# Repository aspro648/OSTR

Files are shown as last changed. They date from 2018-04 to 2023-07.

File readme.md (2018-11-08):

Open Source Turtle Robot (OSTR)
-------------------------------

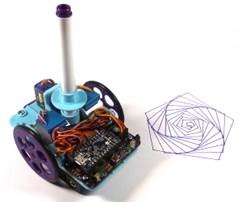
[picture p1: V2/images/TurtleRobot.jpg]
ChickTech Robot
 
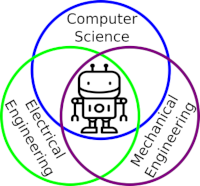
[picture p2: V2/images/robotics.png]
Robotics Engineering Fields
 

I designed this project for a 10-hour workshop for [ChickTech.org](http://www.chicktech.org) whose goal is to introduce teenage women to STEM topics. The goals for this project were:

- Easy to build.
- Easy to program.
- Did something interesting.
- Low-cost so participants could take it home and continue to learn.

Robotics is the exciting intersection of a number of engineering fields including mechanical engineering, electrical engineering, and computer science. This project was designed to make learning about these fields accessible and exciting.

Turtle robots are controled by simple instructions like "forward(distance)" and "left(degrees)", and their visual tracks are instructive as well as entertaining. They also demonstrate how systems with simple rules can have complex behaviors, something we see in nature all the time.

New to Version 2 is the shift from the Adafruit [Trinket Pro](https://www.adafruit.com/product/2010) to their [ItsyBitsy 32U4 3V](https://www.adafruit.com/product/3675) which enables USB communication for easier troubleshooting, or the [ItsyBitsy M0 Express](https://www.adafruit.com/product/3727) which allows programing in Python!

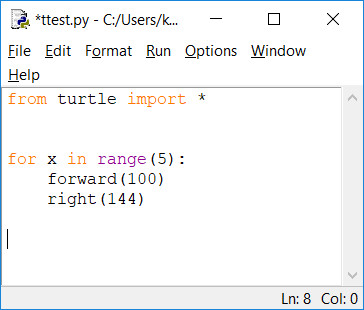
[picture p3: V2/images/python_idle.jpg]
Turtle Python commands in Idle
 
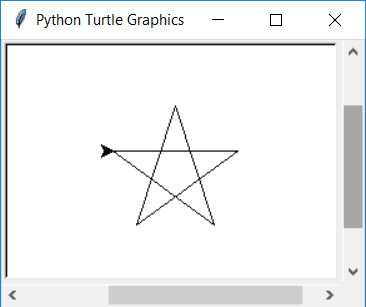
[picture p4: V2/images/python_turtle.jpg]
Turtle Graphics
 

Python is a popular and easy to learn programming language that already has Turle Graphics built in.  Since the robots instructions are the same, programs and paterns can be evaluated on the computer and then run on the robot. 
```python
from turtle import *

for x in range(5):
    forward(100)
    right(144)
```

Here is a great Hour of Code tutorial to get you introduced to Python Turtle: [https://groklearning.com/hoc/activity/snowflake/](https://groklearning.com/hoc/activity/snowflake/).  The only thing pysical Turtle Robot can't do is change colors automatically, but you can alway swap the pens around manually.

### Video of Turtle Robot (V1) in action:

IMAGE ALT TEXT HERE (https://www.youtube.com/watch?v=j0FpB0iv0v0)

This robot has been refined through a number workshops, but still has room for improvement.  Please share your ideas and modifications so it can continue to improve.

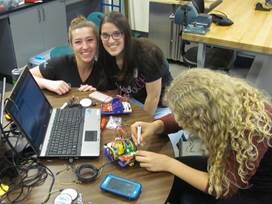
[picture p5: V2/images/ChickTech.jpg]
ChickTech Workshop
 

Bill Of Materials
-----------------
In bulk quantities, the cost per robot is about $40.  The Bill of Materials is available [here](/V2/BOM.md).
Having told you the at-cost and provided you my BOM, I'd still offer to [sell you a kit](https://www.tindie.com/products/MakersBox/open-source-turtle-robot-ostr/) if you'd like to pay for the convenience of a single-source or you don't have access to a 3D printer.  This also allows me continue development for future workshops.

Tindie

Design Files
------------
The electronics were designed using Open Source [KiCad](http://kicad-pcb.org/). Design files are located in the [design_files](V2/design_files/) folder.  You can oogle the [schematic](V2/docs/Schematic.pdf).

The 3D Design files were created with a combination of [FreeCad](https://www.freecadweb.org/), [OpenSCAD](https://www.openscad.org/) (both Open Source), and online [TinkerCad](https://www.tinkercad.com/).  Design files and STLs are located in the [3D](V2/3D/) folder.

Firmware
--------
This project is programed using Open Source [Arduino](https://www.arduino.cc/) or Adafruit's [Circuit Python](https://learn.adafruit.com/welcome-to-circuitpython/what-is-circuitpython) depending on the microcontroller used. The firmware is located in the [firmware](V2/firmware/) folder.  Instructions for setting up the Arduino environment for the ItsyBitsy 32U4 are at [https://learn.adafruit.com/introducting-itsy-bitsy-32u4/](https://learn.adafruit.com/introducting-itsy-bitsy-32u4/).

Assembly Instructions
---------------------
[https://www.instructables.com/id/OSTR/](https://www.instructables.com/id/OSTR/).  
Also, check the [docs](V2/docs/) folder for handouts, etc.  May still have pictures of V1 assembly, but they are nearly identical.

License
-------
[Attribution-ShareAlike 3.0 United States (CC BY-SA 3.0 US)](https://creativecommons.org/licenses/by-sa/3.0/us/)

You are free to:

- Share — copy and redistribute the material in any medium or format
- Adapt — remix, transform, and build upon the material

Under the following terms:

- Attribution — You must give appropriate credit, provide a link to the license, and indicate if changes were made. You may do so in any reasonable manner, but not in any way that suggests the licensor endorses you or your use.
- ShareAlike — If you remix, transform, or build upon the material, you must distribute your contributions under the same license as the original.

Certified Open Source:
----------------------
This project as been certified by the [Open Source Hardward Association](https://certification.oshwa.org/):

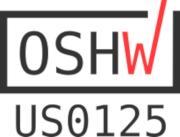
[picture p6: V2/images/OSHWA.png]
OSHWA


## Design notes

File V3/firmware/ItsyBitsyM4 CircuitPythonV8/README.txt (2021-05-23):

Turtle Robot (V2.2) https://github.com/aspro648/OSTR/
@TheMakersBox
#TurtleRobot
648.ken@gmail.com

You have an Adafruit ItsyBitsy M4:
    https://learn.adafruit.com/introducing-adafruit-itsybitsy-m4
Running CiruitPython version 6.2.0
    https://circuitpython.org/board/itsybitsy_m4_express/
With libraries from adafruit-circuitpython-bundle-6.x-mpy-20210521.zip:
    https://github.com/adafruit/Adafruit_CircuitPython_Bundle/releases
Download Mu Editor at https://codewith.mu/en/download

Workshop Links:
  Handouts: https://github.com/aspro648/OSTR/raw/master/V2/docs/Robotics_Handouts.pdf
  Mechanical Assembly: https://github.com/aspro648/OSTR/raw/master/V2/docs/Mechanical_Assembly.pdf
  Name Plate Design: https://github.com/aspro648/OSTR/raw/master/V2/docs/Name_Plate_3D_Design.pdf

Activites:
  https://groklearning.com/hoc/activity/snowflake/
  https://studio.code.org/s/frozen/stage/1/puzzle/1

#############################
CircuitPython Quick Start:

Changing the code is as easy as editing code.py in your favorite text editor. 

Our recommended editor is Mu, which is great for simple projects, and comes
with a built in REPL serial viewer! It is available for Mac, Windows & Linux
https://learn.adafruit.com/welcome-to-circuitpython/installing-mu-editor

After the file is saved, CircuitPython will automatically reload the latest 
code. Try enabling the single-button keyboard!
         (HINT: look for the "# optional! uncomment below..." text)

Connecting to the serial port will give you access to sensor information, 
better error messages and an interactive CircuitPython (known as the REPL). 
On Windows we recommend Mu, Tera Term or PuTTY. 
On Mac OSX and Linux, use Mu or 'screen' can be used from a terminal.

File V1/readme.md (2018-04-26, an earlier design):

Open Source Turtle Robot (OSTR)
============

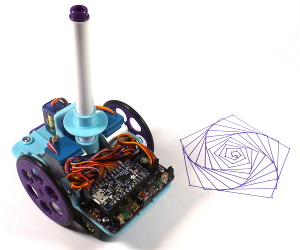
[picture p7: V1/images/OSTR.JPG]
Open Source Turtle Robot
 

Robotics is the exciting intersection of a number of engineering fields including mechanical engineering, electrical engineering, and computer science.  This project was designed as the basis for a two-day workshop for high school age students to introduce them to engineering principles and giving them a jumping off point for exploring their interests further.  There is something for everyone here, even if it is just for the art it creates. The design goals were:

- Easy to build.
- Easy to program.
- Did something interesting.
- Low-cost so participants could take it home and continue to learn.

With those goals in mind, here were a couple of the design choices:

- Arduino compatible for ease of programming.
- 4xAA battery power for cost and availability.
- Stepper motors for accurate motion.
- 3D Printed for ease of customization.
- Pen plotting with Turtle graphics for interesting output.
- Open Source so you could make one of your own!

A kit for this project is [available on Tindie](https://www.tindie.com/products/MakersBox/open-source-turtle-robot-ostr/).
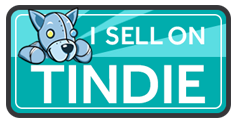
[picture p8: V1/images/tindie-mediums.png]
Tindie Dog (https://www.tindie.com/products/MakersBox/open-source-turtle-robot-ostr/)


Bill Of Materials
-----------------

- [Bill of Materials](BOM.md)

Design Files
------------
The electronics were designed using Open Source [KiCad](http://kicad-pcb.org/). Design files are located in the [electronics](electronics/) folder.  You can oogle the [schematic](electronics/project.pdf).

All 3D STL files located in the [mechanical/STL](mechanical/STL) folder. They were design were designed using:

- [OpenSCAD](http://www.openscad.org/), files located in the [mechanical/OpenSCAD](mechanical/OpenSCAD) folder.
- [FreeCad](https://www.freecadweb.org/), files located in the [mechanical/FreeCad](mechanical/FreeCad) folder.
- [TinkerCad](https://www.tinkercad.com/things/1PzjMSYXagP-oser/editv2) 

Firmware
--------
This project is programed using the Open Source [Arduino](https://www.arduino.cc/). The firmware is located in the [firmware](firmware/) folder.  Instructions for setting up the Arduino enviroment for the Adafruit Trinket Pro are at [https://learn.adafruit.com/introducing-pro-trinket](https://learn.adafruit.com/introducing-pro-trinket).

Assembly Instructions
---------------------
I have published detailed instructions on Instructables at [https://www.instructables.com/id/OSTR/](https://www.instructables.com/id/OSTR/).

License
-------
[Attribution-ShareAlike 3.0 United States (CC BY-SA 3.0 US)](https://creativecommons.org/licenses/by-sa/3.0/us/)

You are free to:

- Share — copy and redistribute the material in any medium or format
- Adapt — remix, transform, and build upon the material

Under the following terms:

- Attribution — You must give appropriate credit, provide a link to the license, and indicate if changes were made. You may do so in any reasonable manner, but not in any way that suggests the licensor endorses you or your use.
- ShareAlike — If you remix, transform, or build upon the material, you must distribute your contributions under the same license as the original.

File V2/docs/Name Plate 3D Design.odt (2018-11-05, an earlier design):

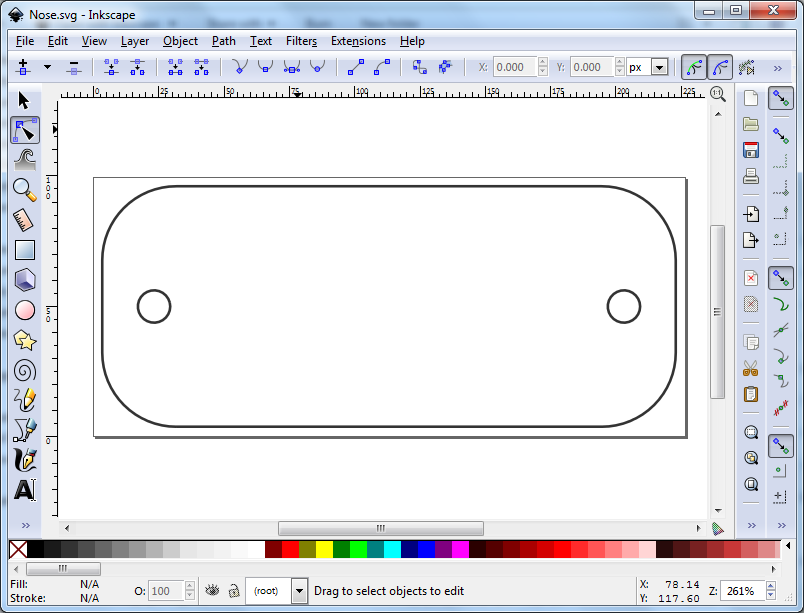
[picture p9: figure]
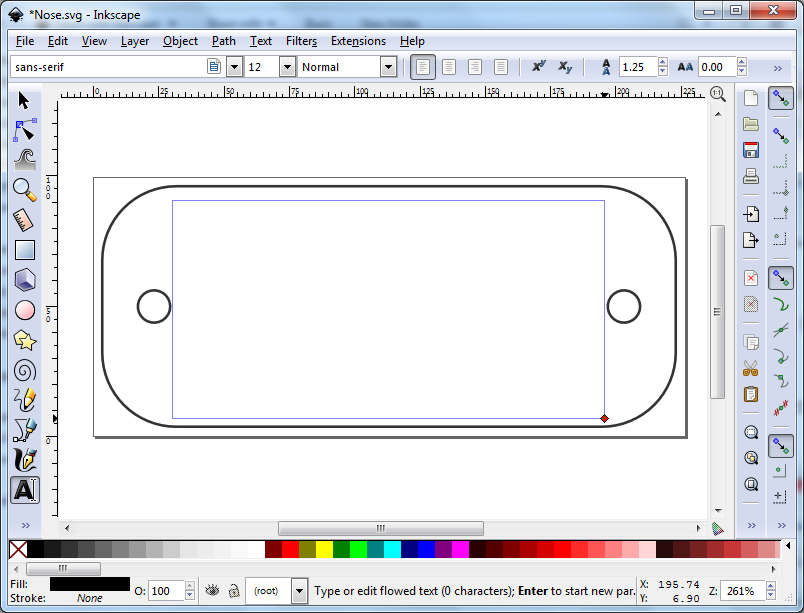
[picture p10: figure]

Launch Inskcape application. Open File “Name_Plate.svg” file. | Click the “A” icon (“Create and Edit Text”) on the left panel and use your mouse to crate a text area within the badge area.

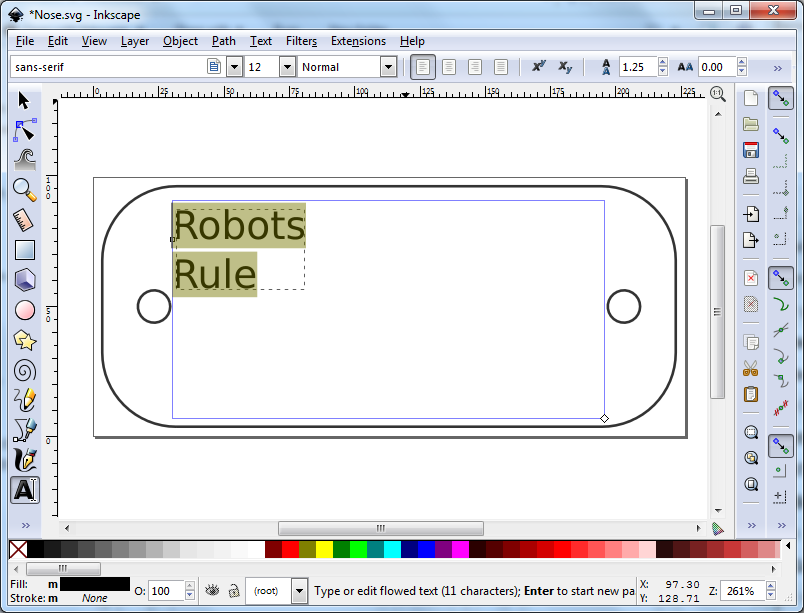
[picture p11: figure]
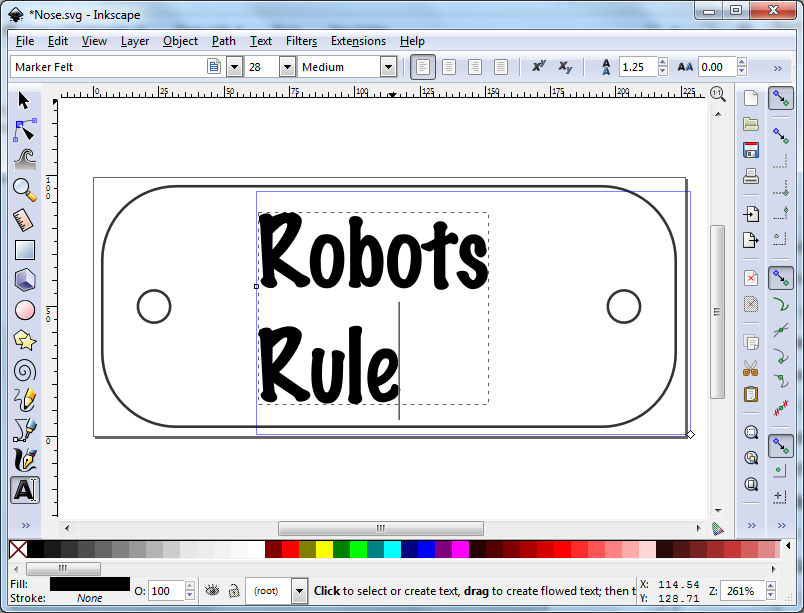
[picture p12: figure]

Type your text in the area. | Select the text with your mouse and then pick the Font and Size you want.

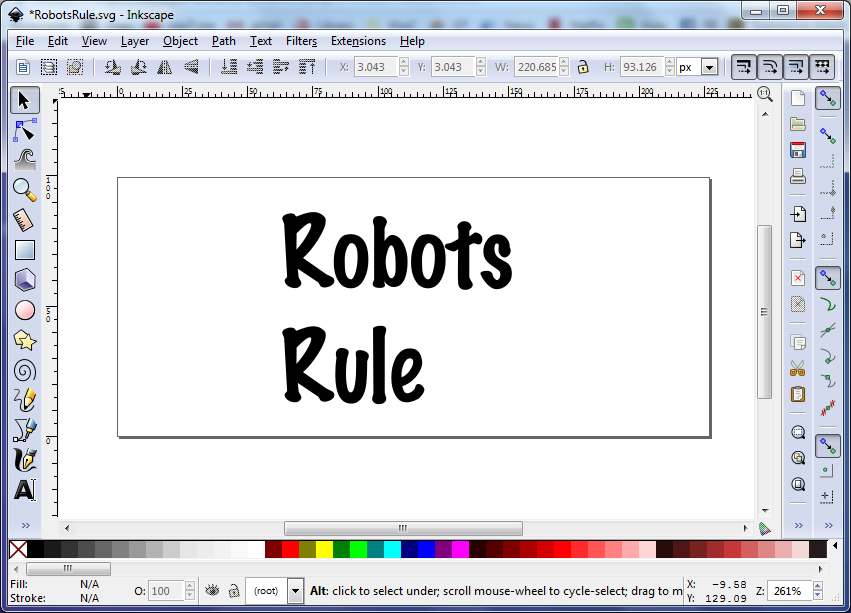
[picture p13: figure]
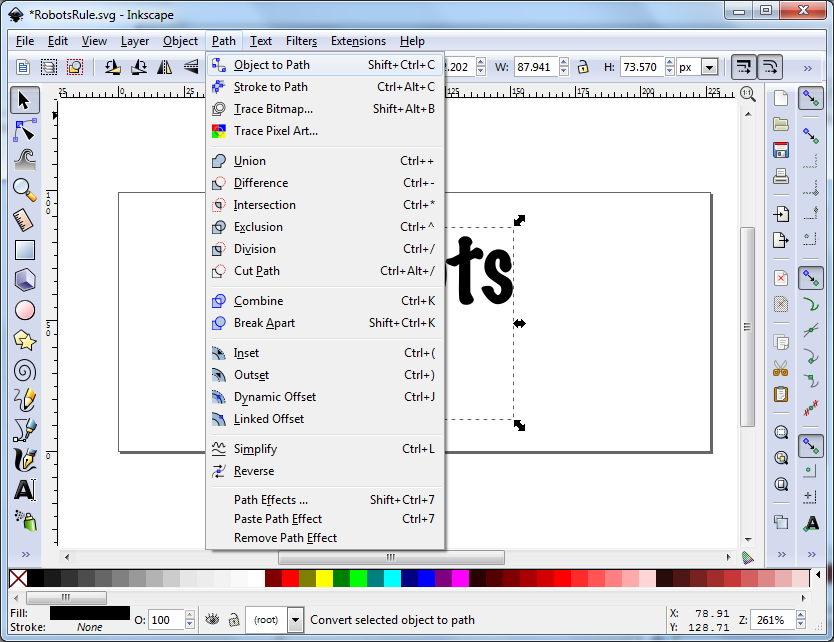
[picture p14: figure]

Select the original badge outline and click delete. “delete”. | Click on the text box again and select “Path” → “Object to Path”.

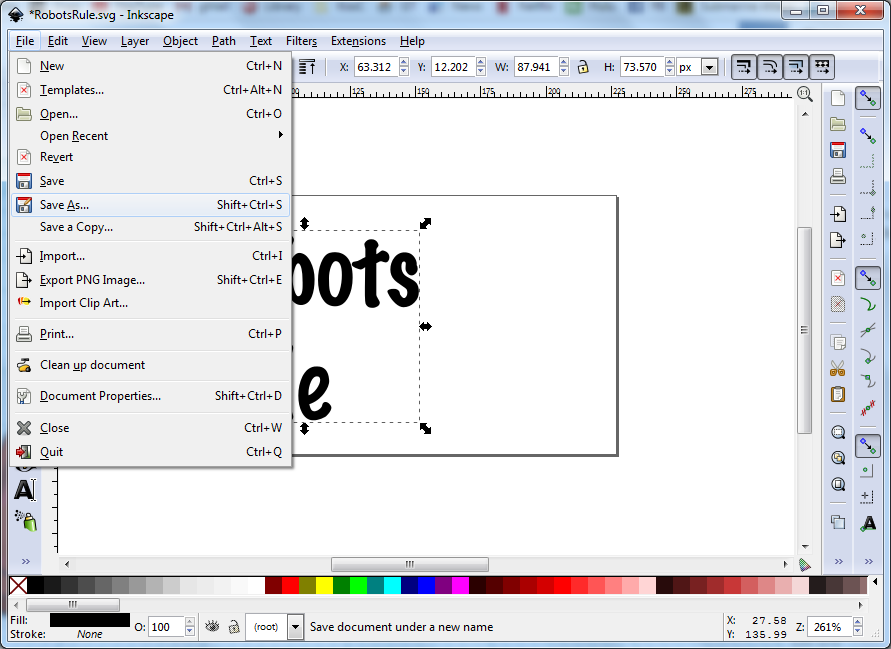
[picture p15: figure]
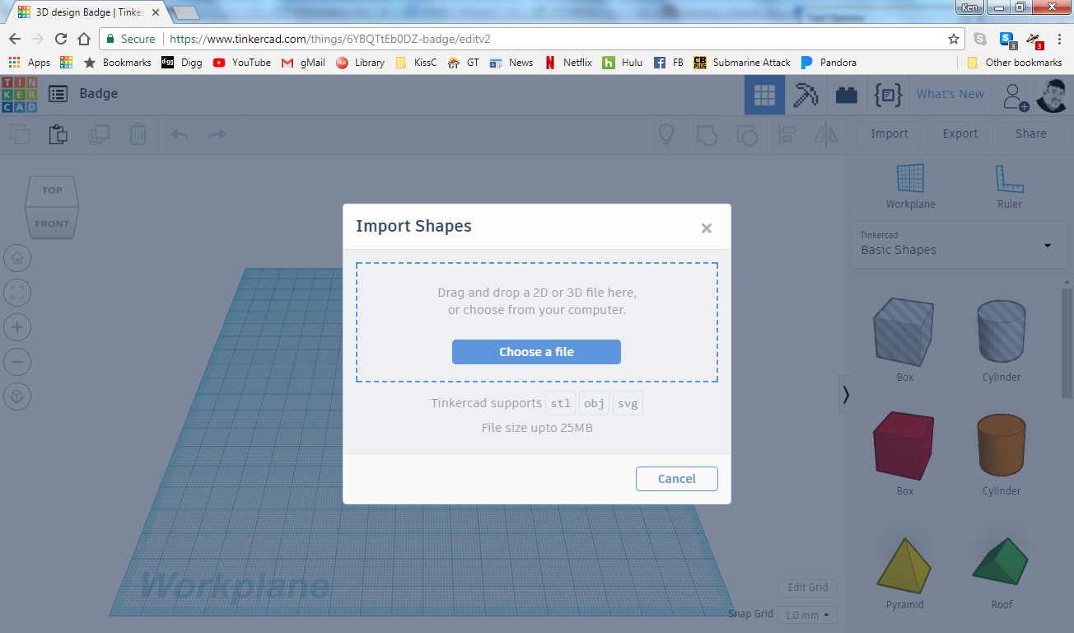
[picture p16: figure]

Select [File] → [Save As] → Select a unique SVG file name. | If needed, sign into TinkerCad.com: User: makers.coderdojo@gmail.com Password: cltm2015 Start a new project. Select [Import] →”Name_Plate.stl”.

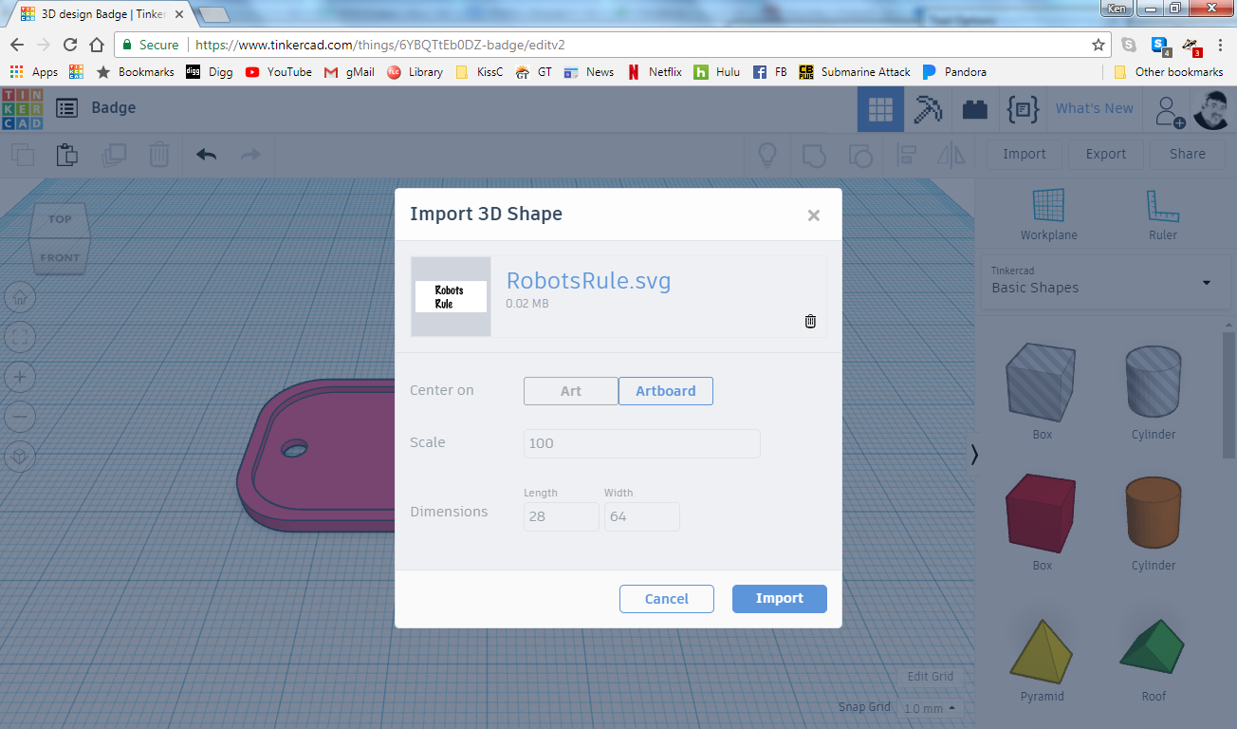
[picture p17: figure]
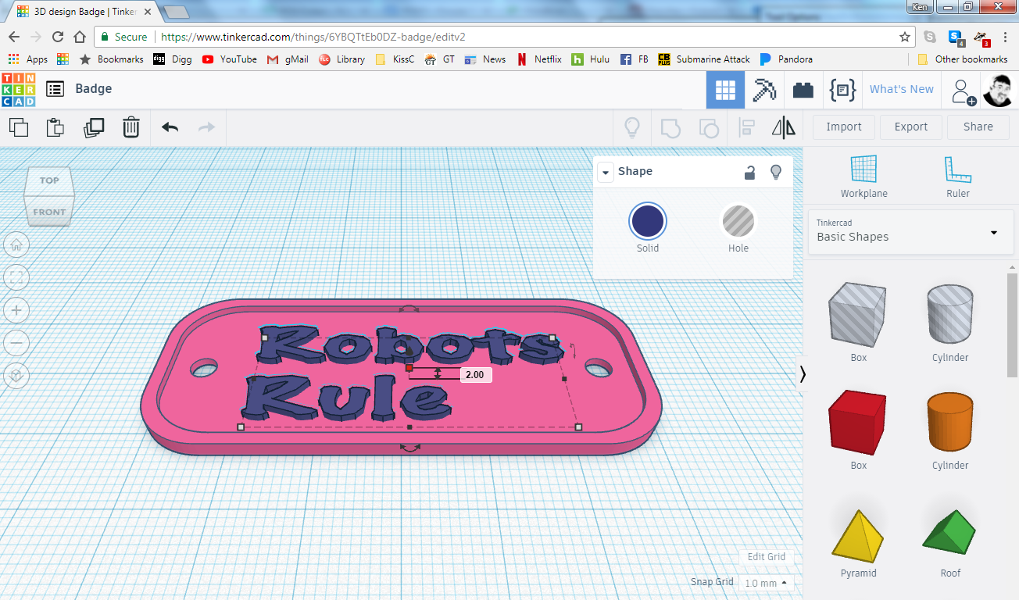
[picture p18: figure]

Select [Import] → Unique svg file you saved earlier. | Repostion and resize text to fit inside of the badge shape. Make the text size 2mm tall.

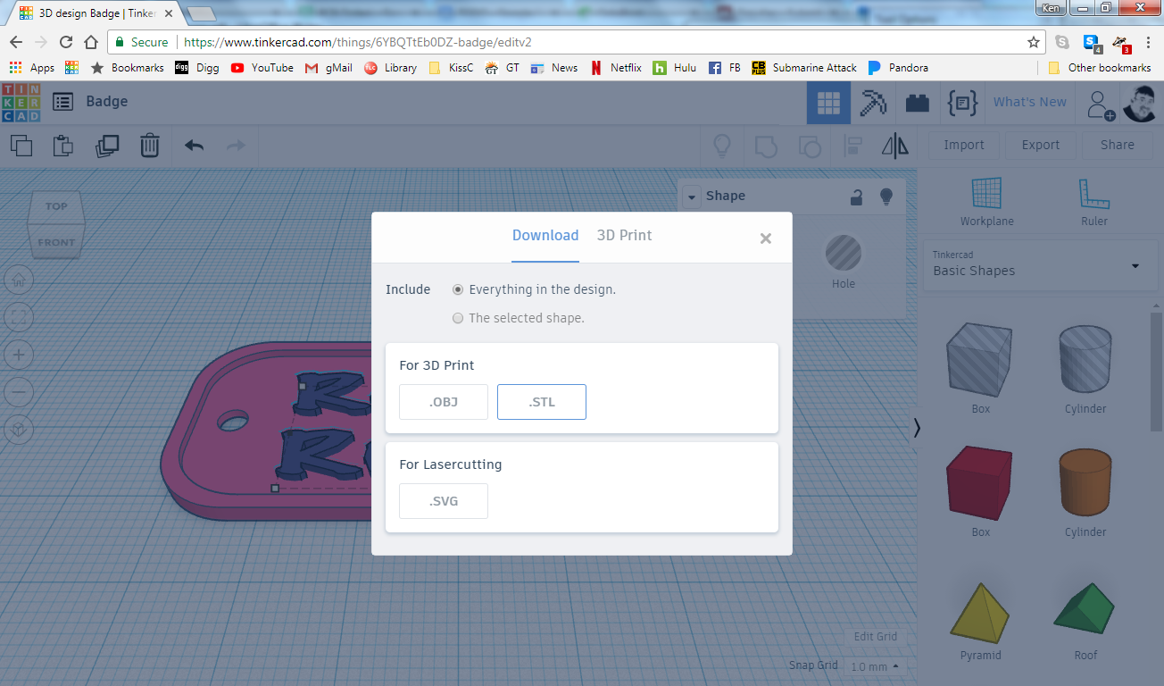
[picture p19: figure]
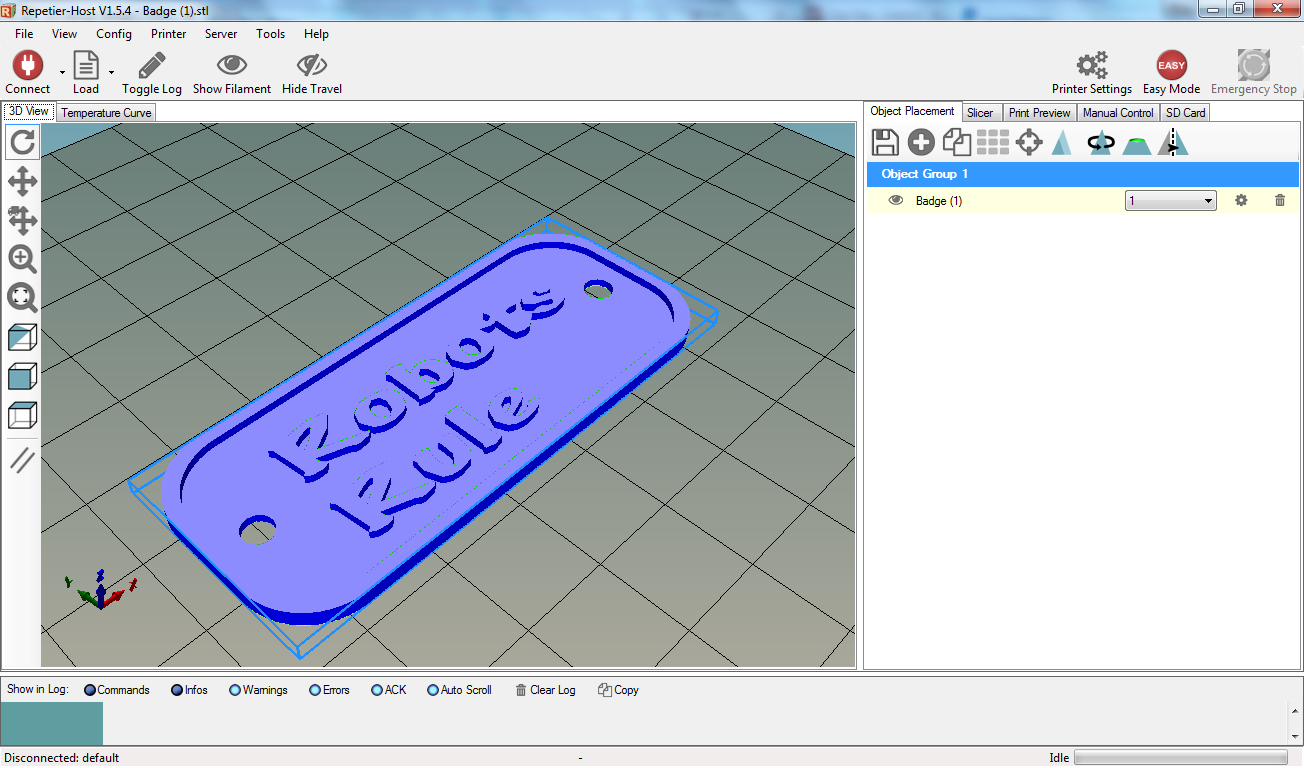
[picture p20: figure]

Select [Export]. Ensure “Everything in Design” is checked. Click “STL” button. | Open the downloaded STL file in your slicer software to verify you are getting what you wanted!

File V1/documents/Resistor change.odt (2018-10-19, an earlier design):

Resistor substitutions to improve obstacle detection: 100 ohm → 47 ohm (yel-purp-black-gold) 10K ohm → 22K ohm (red-red-orange-gold) | Resistor substitutions to improve obstacle detection: 100 ohm → 47 ohm (yel-purp-black-gold) 10K ohm → 22K ohm (red-red-orange-gold)
Resistor substitutions to improve obstacle detection: 100 ohm → 47 ohm (yel-purp-black-gold) 10K ohm → 22K ohm (red-red-orange-gold) | Resistor substitutions to improve obstacle detection: 100 ohm → 47 ohm (yel-purp-black-gold) 10K ohm → 22K ohm (red-red-orange-gold)
Resistor substitutions to improve obstacle detection: 100 ohm → 47 ohm (yel-purp-black-gold) 10K ohm → 22K ohm (red-red-orange-gold) | Resistor substitutions to improve obstacle detection: 100 ohm → 47 ohm (yel-purp-black-gold) 10K ohm → 22K ohm (red-red-orange-gold)
Resistor substitutions to improve obstacle detection: 100 ohm → 47 ohm (yel-purp-black-gold) 10K ohm → 22K ohm (red-red-orange-gold) | Resistor substitutions to improve obstacle detection: 100 ohm → 47 ohm (yel-purp-black-gold) 10K ohm → 22K ohm (red-red-orange-gold)
Resistor substitutions to improve obstacle detection: 100 ohm → 47 ohm (yel-purp-black-gold) 10K ohm → 22K ohm (red-red-orange-gold) | Resistor substitutions to improve obstacle detection: 100 ohm → 47 ohm (yel-purp-black-gold) 10K ohm → 22K ohm (red-red-orange-gold)

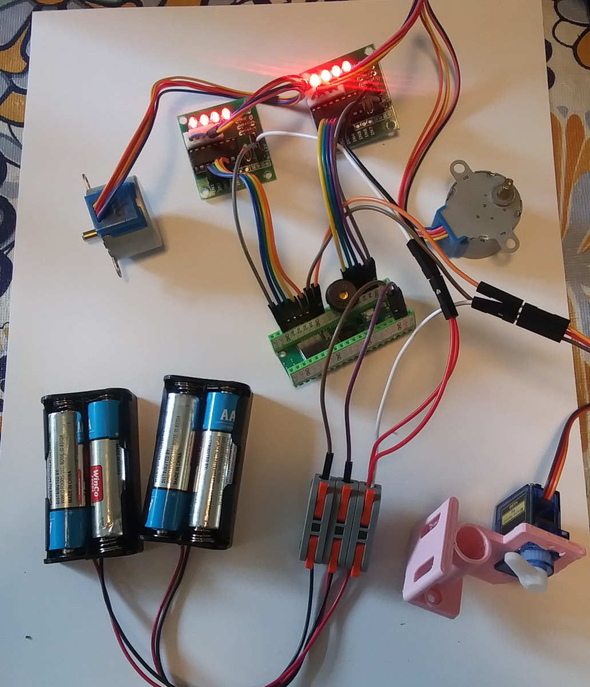
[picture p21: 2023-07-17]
V3/images/proof-of-concept.jpg

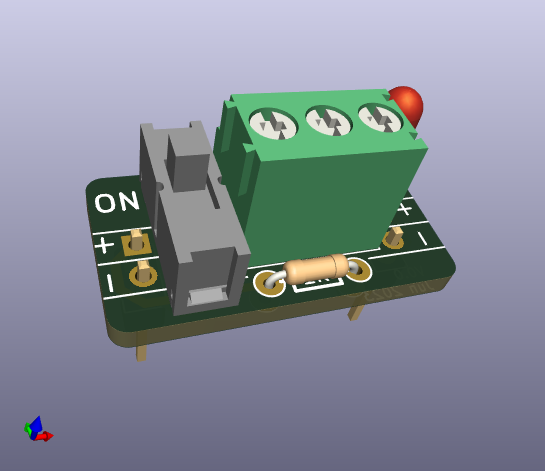
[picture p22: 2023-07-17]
V3/electrical/design_files_KiCAD_V6 BRDBD_PWR/project.png

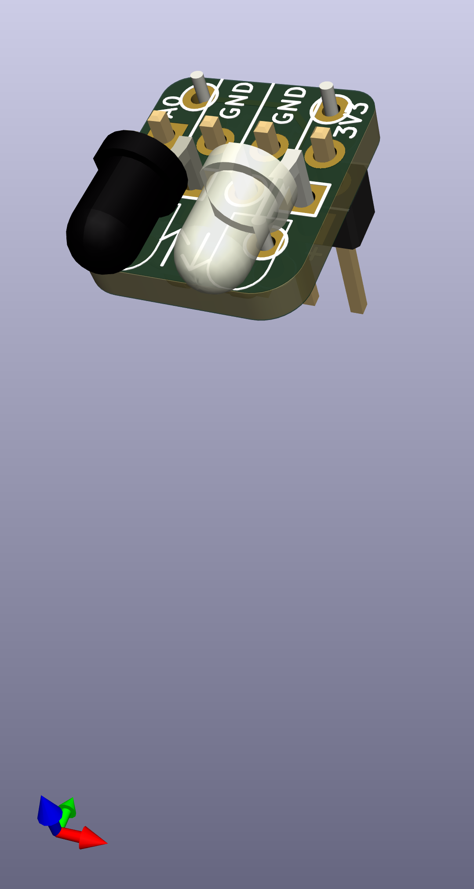
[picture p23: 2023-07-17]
V3/electrical/design_files_KiCAD_V6 BRDBD_IR R/project.png

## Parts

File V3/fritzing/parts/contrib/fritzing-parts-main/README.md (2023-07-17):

# fritzing-parts
My own Fritzing parts repository, ready to be used.

## EXAMPLE
A 28BYJ-48 Unipolar Stepper Motor with its ULN2003 Driver Module attached, mounted with an Arduino UNO.

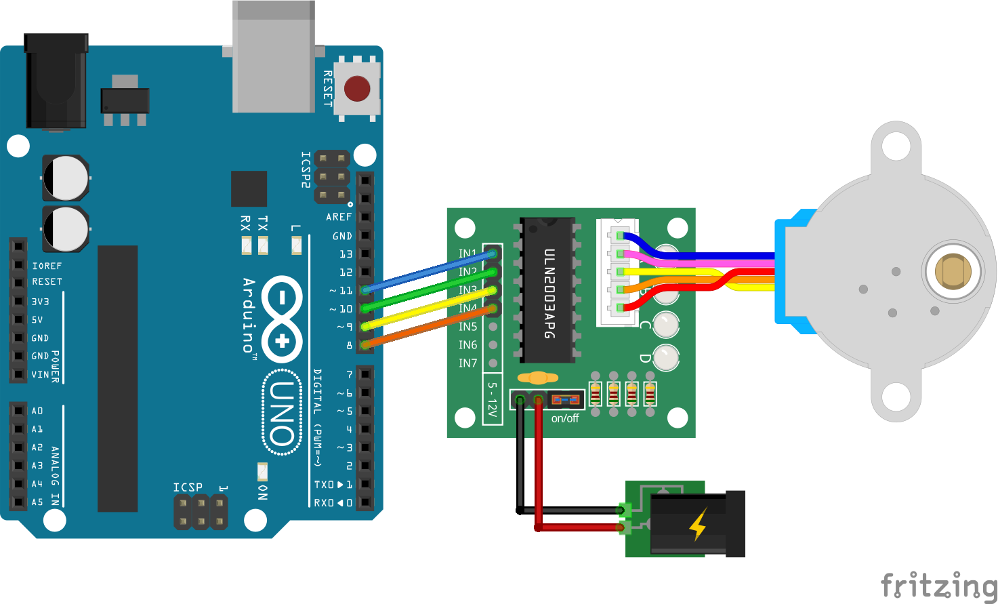
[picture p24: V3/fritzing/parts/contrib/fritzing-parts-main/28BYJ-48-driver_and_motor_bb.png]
28BYJ-48-driver_and_motor_bb


Download [this fritzing example](28BYJ-48-driver_and_motor.fzz).

## LICENSE
This work is licensed under the [GNU General Public License v3.0](LICENSE-GPLV30). All media and data files that are not source code are licensed under the [Creative Commons Attribution 4.0 BY-SA license](LICENSE-CCBYSA40).

More information about licenses in [Opensource licenses](https://opensource.org/licenses/) and [Creative Commons licenses](https://creativecommons.org/licenses/).

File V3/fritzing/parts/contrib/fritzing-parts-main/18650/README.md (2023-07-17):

# Rechargable 3.7V 18650 Li-ion cell

A Fritzing part of a rechargable battery, 3.7V 18650 Li-ion cell, based on [the work of Dr Kristofer Chan](https://github.com/DrKrisChan/18650-Fritzing-part).

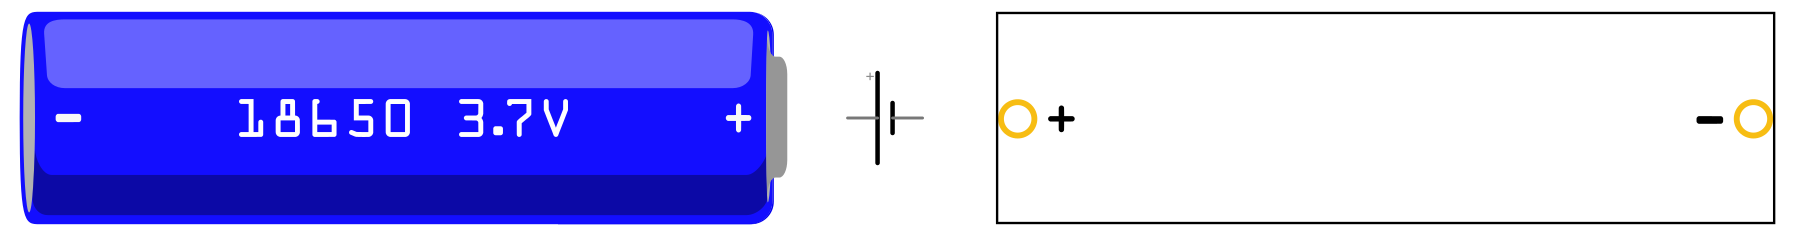
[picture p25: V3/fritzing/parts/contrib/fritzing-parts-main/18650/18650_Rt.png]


\[[Download link](18650_Rt.fzpz)\]

## LICENSE

This work is licensed under the [GNU General Public License v3.0](../LICENSE-GPLV30). All media and data files that are not source code are licensed under the [Creative Commons Attribution 4.0 BY-SA license](../LICENSE-CCBYSA40).

More information about licenses in [Opensource licenses](https://opensource.org/licenses/) and [Creative Commons licenses](https://creativecommons.org/licenses/).

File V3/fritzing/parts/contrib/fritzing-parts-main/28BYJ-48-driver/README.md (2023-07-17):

# 28BYJ-48 Driver Module ULN2003
A fritzing part for the 28BYJ-48 Driver Module ULN2003 with its JST connector and all the control and power pins. Includes also the schematic symbol and the pcb footprint.

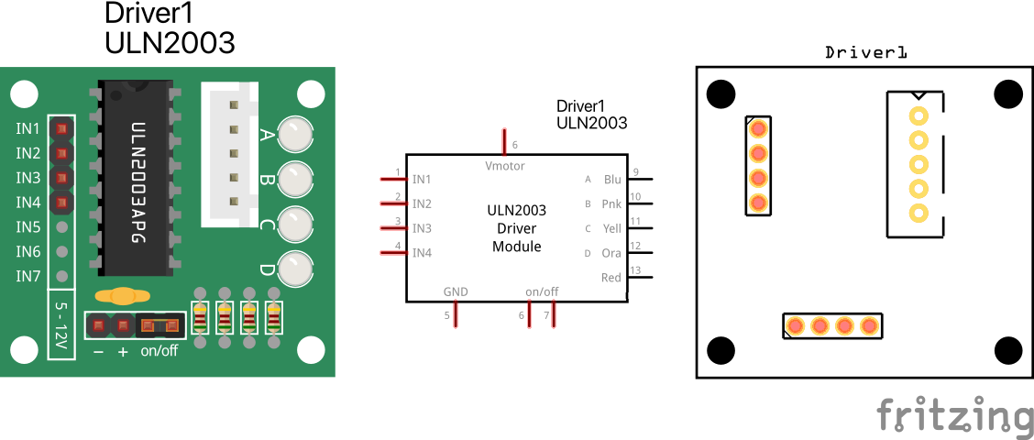
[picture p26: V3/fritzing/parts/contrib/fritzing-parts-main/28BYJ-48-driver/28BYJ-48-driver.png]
28BYJ-48-driver


Have a look at the [28BYJ-48 Stepper Motor part](../28BYJ-48-motor/) also.

## NOTES

* The JST connector pins are incorrectly marked as **female** on purpose, as a trick to *help* Fritzing connect the 28BYJ-48 Unipolar Stepper Motor to it more *naturally* (the same trick is applied to the motor itself).

* Used some of [the fritzing tools by @Vanepp](https://github.com/vanepp): go check them.

## LICENSE

This work is licensed under the [GNU General Public License v3.0](../LICENSE-GPLV30). All media and data files that are not source code are licensed under the [Creative Commons Attribution 4.0 BY-SA license](../LICENSE-CCBYSA40).

More information about licenses in [Opensource licenses](https://opensource.org/licenses/) and [Creative Commons licenses](https://creativecommons.org/licenses/).

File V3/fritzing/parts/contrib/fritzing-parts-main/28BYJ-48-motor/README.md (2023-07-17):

# 28BYJ-48 Stepper Motor
A fritzing part for the 28BYJ-48 Stepper Motor with its JST connector and all the wiring done correctly. Includes also the schematic symbol and the pcb footprint.

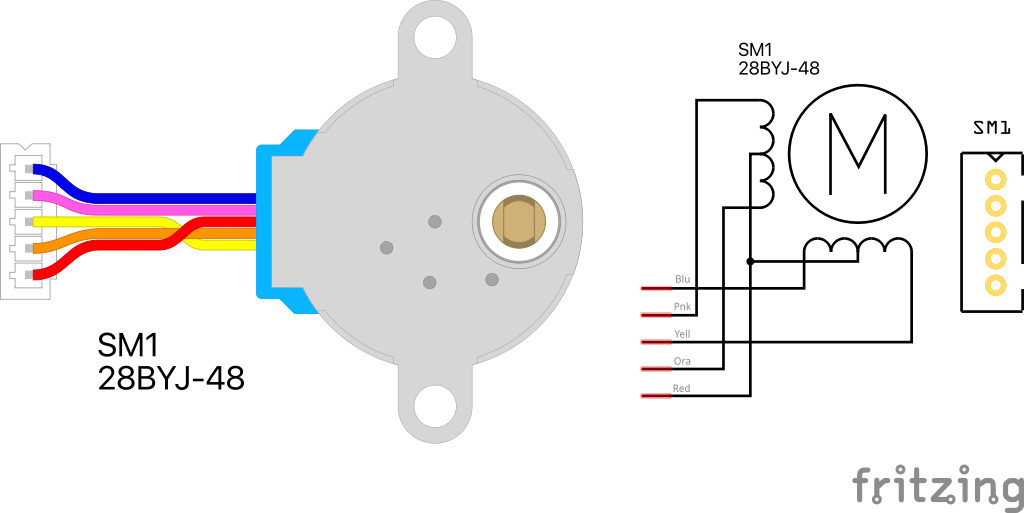
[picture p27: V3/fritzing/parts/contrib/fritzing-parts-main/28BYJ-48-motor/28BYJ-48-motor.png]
28BYJ-48-motor


Have a look at the [28BYJ-48 ULN2003 driver module part](../28BYJ-48-driver/) also.

## NOTES

* The connector pins are incorrectly marked as **male** on purpose as a trick to *help* Fritzing connect it to the driver module more easily (where the inverse trick is applied).

* Used some of [the fritzing tools by @Vanepp](https://github.com/vanepp): go check them.

## LICENSE

This work is licensed under the [GNU General Public License v3.0](../LICENSE-GPLV30). All media and data files that are not source code are licensed under the [Creative Commons Attribution 4.0 BY-SA license](../LICENSE-CCBYSA40).

More information about licenses in [Opensource licenses](https://opensource.org/licenses/) and [Creative Commons licenses](https://creativecommons.org/licenses/).

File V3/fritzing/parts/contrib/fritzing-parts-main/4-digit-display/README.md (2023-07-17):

# 4-digit 7-segment LED display

Two fritzing parts of a 4-digit 7-segment LED display module driven by a TM1637 IC controller via 1-wire protocol (a simplified version of I2C protocol):

* [Robotdyn version](4-digit-display_8pingreen_Rt.fzpz) with duplicate 4-pin rows, in green color
* [HiLetgo version](4-digit-display_4pinred_Rt.fzpz) with a single 4-pin row, in red color

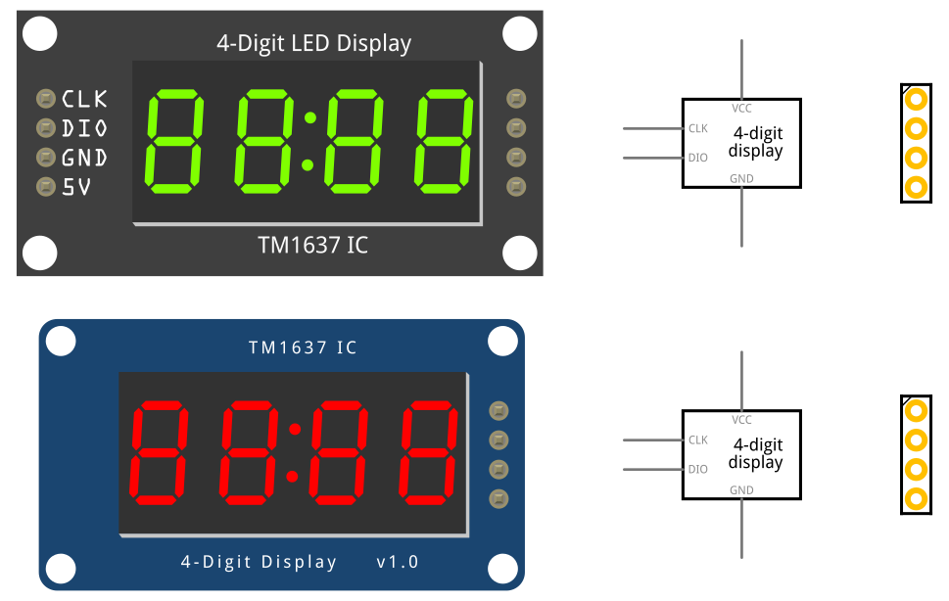
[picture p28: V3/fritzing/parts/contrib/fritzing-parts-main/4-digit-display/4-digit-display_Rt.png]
4-digit-display


## LICENSE

This work is licensed under the [GNU General Public License v3.0](../LICENSE-GPLV30). All media and data files that are not source code are licensed under the [Creative Commons Attribution 4.0 BY-SA license](../LICENSE-CCBYSA40).

More information about licenses in [Opensource licenses](https://opensource.org/licenses/) and [Creative Commons licenses](https://creativecommons.org/licenses/).

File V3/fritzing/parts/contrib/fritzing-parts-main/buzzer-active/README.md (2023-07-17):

# Active buzzer 12mm, 3-5V
A fritzing part of an active buzzer of 12mm diameter and 3-5V, without a breakout board and with bendable legs.

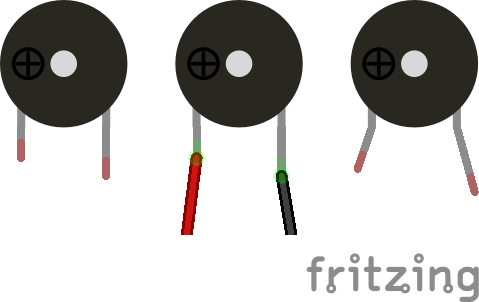
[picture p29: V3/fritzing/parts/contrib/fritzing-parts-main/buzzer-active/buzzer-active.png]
active buzzer


## LICENSE

This work is licensed under the [GNU General Public License v3.0](../LICENSE-GPLV30). All media and data files that are not source code are licensed under the [Creative Commons Attribution 4.0 BY-SA license](../LICENSE-CCBYSA40).

More information about licenses in [Opensource licenses](https://opensource.org/licenses/) and [Creative Commons licenses](https://creativecommons.org/licenses/).

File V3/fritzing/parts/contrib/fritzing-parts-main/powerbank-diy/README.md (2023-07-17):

# Modded Powerbank-DIY 5V
A fritzing part of a Powerbank-DIY (do it yourself) modded with dupont cables as refected in [this guide (Spanish)](https://www.roboteach.es/modificacion-power-bank/). 5V output with -normally- nice security protections like anti-short-circuit, over-charge and over-discharge.

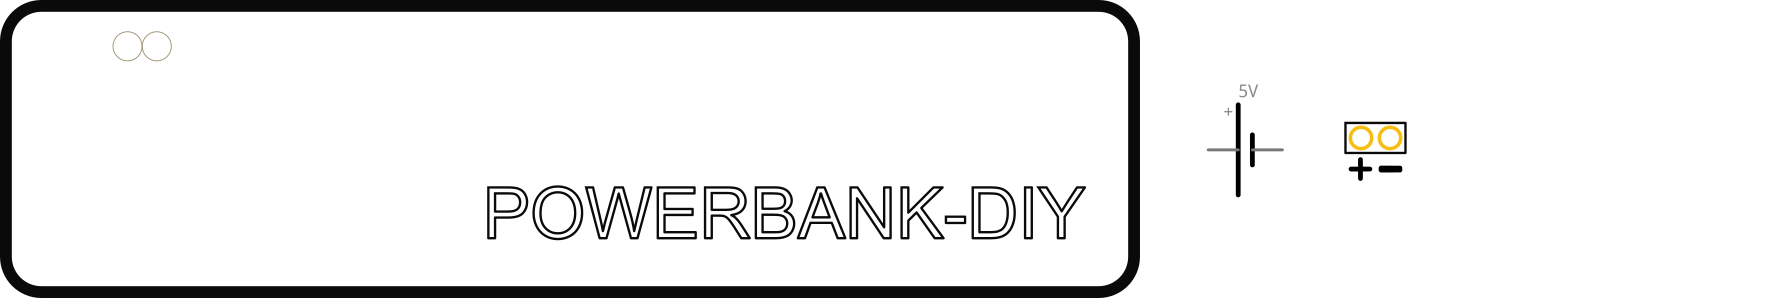
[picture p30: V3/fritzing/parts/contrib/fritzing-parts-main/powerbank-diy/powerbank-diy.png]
powerbank-diy


## LICENSE

This work is licensed under the [GNU General Public License v3.0](../LICENSE-GPLV30). All media and data files that are not source code are licensed under the [Creative Commons Attribution 4.0 BY-SA license](../LICENSE-CCBYSA40).

More information about licenses in [Opensource licenses](https://opensource.org/licenses/) and [Creative Commons licenses](https://creativecommons.org/licenses/).

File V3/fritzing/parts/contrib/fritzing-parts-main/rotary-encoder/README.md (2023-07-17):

# Rotary encoder with push button
A fritzing part of an EC11xx rotary encoder with momentary switch and NO brekout board.

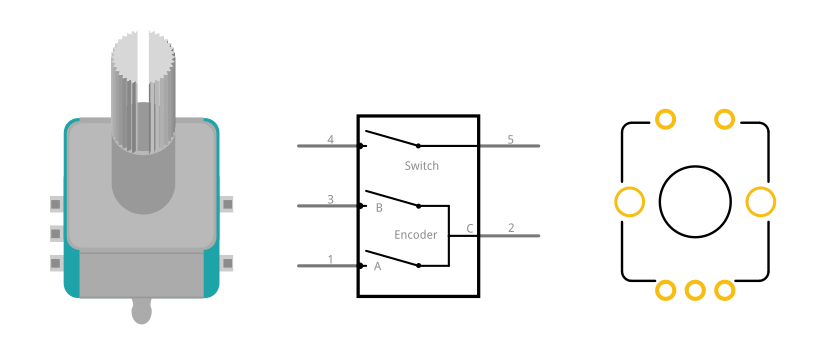
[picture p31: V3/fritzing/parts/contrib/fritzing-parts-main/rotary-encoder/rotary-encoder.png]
rotary_encoder


## LICENSE

This work is licensed under the [GNU General Public License v3.0](../LICENSE-GPLV30). All media and data files that are not source code are licensed under the [Creative Commons Attribution 4.0 BY-SA license](../LICENSE-CCBYSA40).

More information about licenses in [Opensource licenses](https://opensource.org/licenses/) and [Creative Commons licenses](https://creativecommons.org/licenses/).

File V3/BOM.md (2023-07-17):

Open Source Turtle Robot Bill Of Materials (V2)
=================

Turtle Board Kit:

- 1 ea. Park Purfect Purple PCB from /design_files folder
- 1 ea. Microcontroller, either:
  - Adafruit ItsyBitsy M4 (CircuitPython), https://www.digikey.com/short/p01z13 (recommended)
  - Adafruit ItsyBitsy 32U4 3V (Arduino), https://www.digikey.com/short/jw9mwm
- 1 ea. ULN2803 Darlington Driver, [STM ULN2803A](https://www.digikey.com/short/q728f3)
- 1 ea. CONN IC DIP SOCKET 18POS TIN [On Shore ED18DT](https://www.digikey.com/short/jd3rvh) (optional)
- 2 ea. JST B5B-XH-A Receptical, [JST B5B-XH-A](https://www.digikey.com/short/qcrr5m)
- 1 ea. SPST switch, [E-Switch EG1218](https://www.digikey.com/short/qcwd5b)
- 1 ea. Tactitle switch, [TE 1825910-6](https://www.digikey.com/short/q32j9w)
- 2 ea. 14-POS Female header, ‎Sullins PPPC141LFBN-RC‎,https://www.digikey.com/short/p01z83
- 1 ea. pin male header, [Sullins PREC040SAAN-RC](https://www.digikey.com/short/jzr38f)
- 2 ea. TERMINAL 3.5MM 2POS, [On Shore ED555/2DS](http://www.digikey.com/short/7zj1f4)
- 1 ea. 100 uF cap, [Nichicon UMA1E101MDD](https://www.digikey.com/short/jd3rdz)
- 1 ea. 10 uF cap, [Panasonic ECE-A1HKS100](http://www.digikey.com/short/7thwrt)
- 1 ea. 1 uF cap, [AVX SR205E105MAR](http://www.digikey.com/short/747wv0)
- 2 ea. Photo Transistor, https://www.digikey.com/short/jw9ht0
- 2 ea. IR Emitter 940nm 1.2V, https://www.digikey.com/short/jw9m1r
- 4 ea. 330 ohm resistor 1/8W, [Stackpole CF18JT330R](https://www.digikey.com/short/jzr35t)
- 2 ea. 10K resistor 1/8W, 
- 2 ea. 3mm LEDs, [Wurth 151031VS06000](http://www.digikey.com/short/3335hz)
- 1 ea. Piezo speaker, [TDK PS1240P02CT3](https://www.digikey.com/short/zndnmn)

Electromechanical:

- 2 ea. Geared 5V Stepper, [28byj](http://a.co/hwCrUy4)
- 1 ea. Micro servo, [SG 9G](http://www.adafruit.com/products/169
- 2 ea. 2 x AA Holder, [Keystone 2463](http://www.digikey.com/short/tz5bd1)

Hardware Kit:

- 2 ea. 1 5/8" ID x 1/8' (Dash 223) O-ring, https://www.mcmaster.com/9452k61
- 1 ea. Caster 5/8" bearing, http://www.mcmaster.com/#96455k58/=yskbki
- 8 ea. M3 x 6mm rounded head screw, https://www.mcmaster.com/#92005a116/=19rb37d
- 4 ea. M3 x 6mm flat head screw, http://www.mcmaster.com/#91420a116/=yskru0
- 10 ea. M3 Nut, http://www.mcmaster.com/#90591a250/=yskc6u
- 7 ea. #2 x 1/4 thread forming screw, https://www.mcmaster.com/#90380a005/=19o9cmt
- 3 ea. zip-tie, 7130K101	 https://www.mcmaster.com/catalog/129/1800/7130K102

3D Parts:
- 1 ea. cassis
- 2 ea. wheel
- 1 ea. caster
- 2 ea. pen collar

Misc:

- Markers
- Stickers
- Screwdriver
- 4 ea. AA batteries, [Panasonic LR6XWA/B](https://www.digikey.com/short/qcwdbb)   
- 1 ea. USB 2.0 A Male to Micro B cable, http://a.co/bYaNDg6

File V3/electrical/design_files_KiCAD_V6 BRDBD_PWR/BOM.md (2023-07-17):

Open Source Turtle Robot Bill Of Materials (V3)
=================

BOM:

- 1 ea. Park Purfect Purple PCB from /design_files folder

- 1 ea. SPST switch, [E-Switch EG1218](https://www.digikey.com/short/qcwd5b)

- 2 ea. TERMINAL 3.5MM 2POS, [On Shore ED555/2DS](http://www.digikey.com/short/7zj1f4)

- 1 ea. 1K ohm resistor 1/8W

- 1 ea. Diode 1N4001

https://www.digikey.com/en/products/detail/on-shore-technology-inc/OSTTF030161/614573
https://www.digikey.com/en/products/detail/on-shore-technology-inc/ED550-3DS/182971

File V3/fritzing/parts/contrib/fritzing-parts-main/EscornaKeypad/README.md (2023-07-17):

# Escornabot 5 keys Keypad
A fritzing part for the [Escornabot 5 keys Keypad](https://github.com/mgesteiro/escornakeypad) with bendable legs/connectors.

EscornaKeypad

## NOTES

* Part of the [Escornabot project](https://escornabot.org).
* Fritzing part of the [original design](https://github.com/mgesteiro/escornakeypad).
* Used some of [the fritzing tools by @Vanepp](https://github.com/vanepp): go check them.

## LICENSE

This work is licensed under the [GNU General Public License v3.0](../LICENSE-GPLV30). All media and data files that are not source code are licensed under the [Creative Commons Attribution 4.0 BY-SA license](../LICENSE-CCBYSA40).

More information about licenses in [Opensource licenses](https://opensource.org/licenses/) and [Creative Commons licenses](https://creativecommons.org/licenses/).

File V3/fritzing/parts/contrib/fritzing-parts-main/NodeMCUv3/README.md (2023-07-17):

# Lolin NodeMCU v3
A fritzing part of an ESP-8266 Lolin NodeMCU v3 board, based on the [work of Achim Pieters](https://github.com/AchimPieters/Fritzing-Custom-Parts).

NodeMCU

## LICENSE

This work is licensed under the [GNU General Public License v3.0](../LICENSE-GPLV30). All media and data files that are not source code are licensed under the [Creative Commons Attribution 4.0 BY-SA license](../LICENSE-CCBYSA40).

More information about licenses in [Opensource licenses](https://opensource.org/licenses/) and [Creative Commons licenses](https://creativecommons.org/licenses/).

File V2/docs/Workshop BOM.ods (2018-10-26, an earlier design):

EE
Quantity | Manufacturer Part Number | Manufacturer | Digi-Key Part Number | Unit Price | Unit Price Q20 | Extended Price
1 | OSH Park | PCB 1.26 x 2.31 |  |  | 2.9106 | 2.9106
2 | B5B-XH-AM(LF)(SN) | JST Sales America Inc. | 455-2239-ND | 0.26 | 0.243 | 0.486
1 | EG1218 | E-Switch | EG1903-ND | 0.61 | 0.582 | 0.582
2 | ED555/2DS | On Shore Technology Inc. | ED1514-ND | 1.06 | 0.563 | 1.126
2 | 2463 | Keystone Electronics | 36-2463-ND | 1.1 | 0.873 | 1.746
1 | SR205E105MAR | AVX Corporation | 478-7667-ND | 0.84 | 0.63 | 0.63
2 | CF18JT100R | Stackpole Electronics Inc. | CF18JT100RCT-ND | 0.1 | 0.036 | 0.072
2 | CF18JT330R | Stackpole Electronics Inc. | CF18JT330RCT-ND | 0.1 | 0.036 | 0.072
2 | CF18JT10K0 | Stackpole Electronics Inc. | CF18JT10K0CT-ND | 0.1 | 0.036 | 0.072
1 | 30044 | SCS | SCP347-ND | 0.12 | 0.12 | 0.12
2 | 151031VS06000 | Wurth Electronics Inc. | 732-5008-ND | 0.16 | 0.16 | 0.32
1 | 1825910-6 | TE Connectivity ALCOSWITCH Switches | 450-1650-ND | 0.11 | 0.11 | 0.11
2 | PPTC141LFBN-RC | Sullins Connector Solutions | S7012-ND | 0.91 | 0.803 | 1.606
1 | IR204 | Everlight Electronics Co Ltd | 1080-1072-ND | 0.39 | 0.22 | 0.22
1 | PT204-6B | Everlight Electronics Co Ltd | 1080-1151-ND | 0.34 | 0.184 | 0.184
1 | B5B-XH-A(LF)(SN) | JST Sales America Inc. | 455-2270-ND | 0.25 | 0.24 | 0.24
1 | ULN2803A | STMicroelectronics | 497-2356-5-ND | 1.19 | 1.07 | 1.07
1 | ED18DT | On Shore Technology Inc. | ED3047-5-ND | 0.23 | 0.181 | 0.181
1 | ECE-A1HKS100 | Panasonic Electronic Components | P997-ND | 0.27 | 0.187 | 0.187
1 | UMA1E101MDD | Nichicon | 493-14503-ND | 0.33 | 0.23 | 0.23
 |  |  |  |  | Total | $12.16
Mech / Elec
2 | Geared 5V Stepper |  |  |  | 2.358 | 4.716
1 | Micro servo |  |  |  | 1.809 | 1.809
1 | USB 2.0 A Male |  |  |  | 1.1 | 1.1 | 240
1 | Adafruit ItsyBitsy M0 Express |  |  |  | 10.76 | 10.76 | 5
1 | Adafruit screw driver | https://www.adafruit.com/product/3284 |  |  | 1.35 | 1.35
1 | Robot sticker | https://www.adafruit.com/product/622 |  |  | 1.5 | 1.5
8 | AA batteries |  |  |  | 0.276875 | 2.215
31 | 3D Printing | grams | $20/kg |  | 0.02 | 0.62
2 | Roseart finetip |  |  |  | 0.16 | 0.32
1 | 6x4x3 box |  |  |  | 0.48 | 0.48
4 | 22 awg ferrule |  |  |  | 0.03495 | 0.1398
 |  |  |  |  | Total | $25.01
Hardware
2 | - 2 ea. 1 7/8" ID x 3/16' O-ring | http://www.mcmaster.com/#9452k47/=yskfyu |  |  | 0.1948 | 0.3896
1 | - 1 ea. Caster 5/8" bearing | http://www.mcmaster.com/#96455k58/=yskbki |  |  | 0.1636 | 0.1636
8 | - 8 ea. M3 x 6mm rounded head screw | https://www.mcmaster.com/#92005a116/=19rb37d |  |  | 0.0276 | 0.2208
4 | - 4 ea. M3 x 6mm flat head screw | http://www.mcmaster.com/#91420a116/=yskru0 |  |  | 0.024 | 0.096
10 | - 10 ea. M3 Nut | http://www.mcmaster.com/#90591a250/=yskc6u |  |  | 0.0212 | 0.212
4 | - 4 ea. #2 x 1/4 thread forming screw | https://www.mcmaster.com/#90380a005/=19o9cmt |  |  | 0.074 | 0.296
2 | zip ties | https://www.amazon.com/gp/product/B077TJ11JR |  |  | 0.01915 | 0.0383
 |  |  |  |  | Total | $1.42
 |  |  |  | Grand Total |  | $38.59

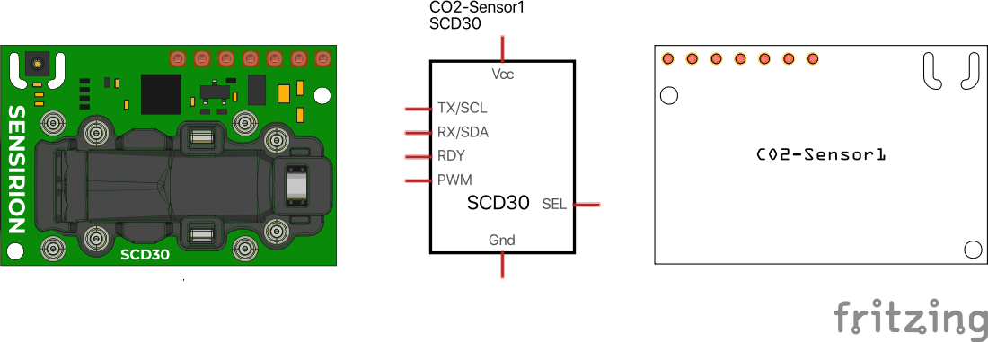
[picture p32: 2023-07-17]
V3/fritzing/parts/contrib/fritzing-parts-main/Sensirion-SCD30/Sensirion-SCD30.png

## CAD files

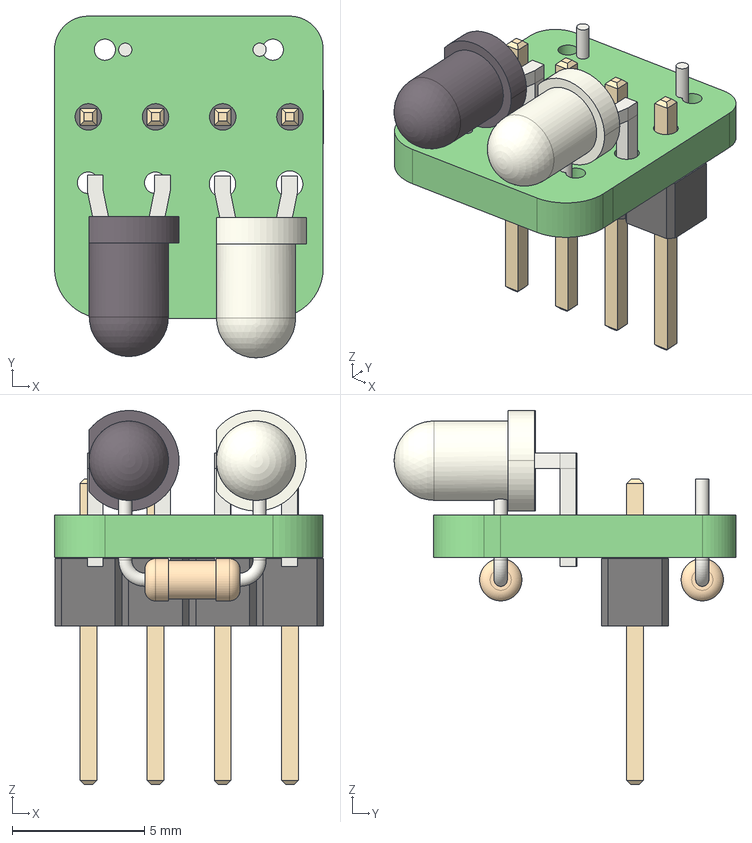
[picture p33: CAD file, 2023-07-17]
V3/electrical/design_files_KiCAD_V6 BRDBD_IR L/project.step
10.2 x 12.9 x 14.1 mm
_autosave-project PCB

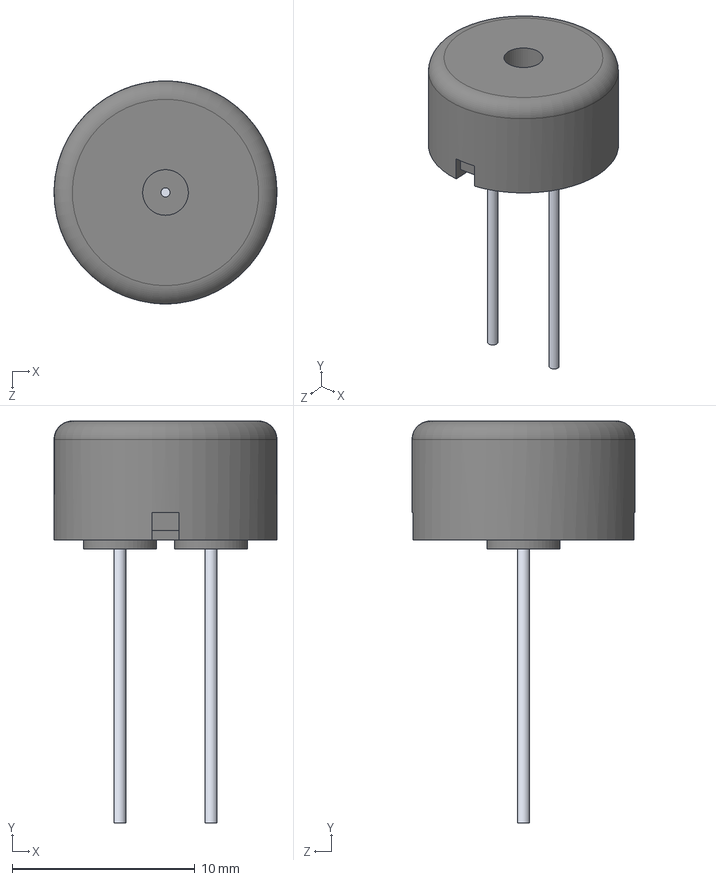
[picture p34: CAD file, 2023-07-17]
V3/electrical/design_files_KiCAD_V6 BRDBD_IR R/3D/PS1240P02CT3.stp
12.2 x 22.0 x 12.2 mm

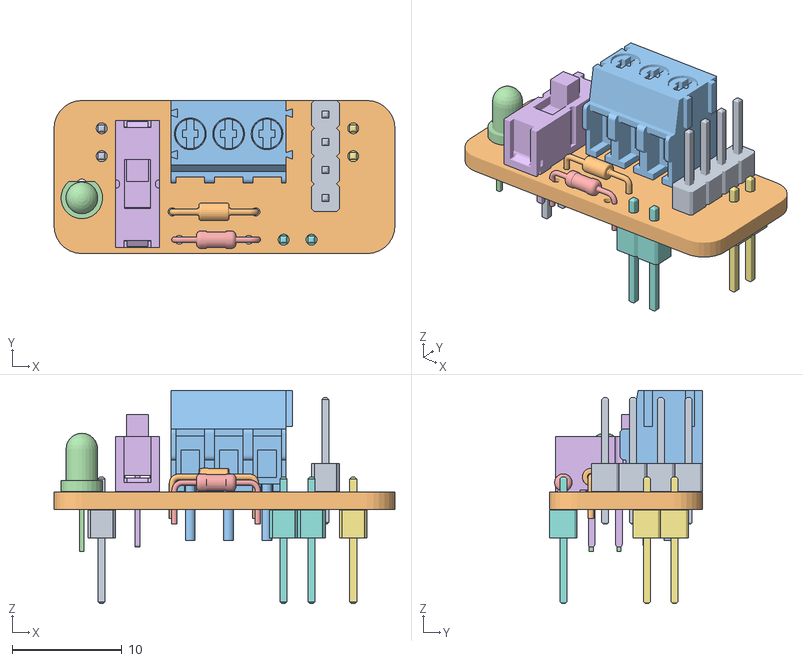
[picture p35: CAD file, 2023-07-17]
V3/electrical/design_files_KiCAD_V6 BRDBD_PWR/BRBD_PWR.obj
31.1 x 14.0 x 19.4
_autosave-project PCB

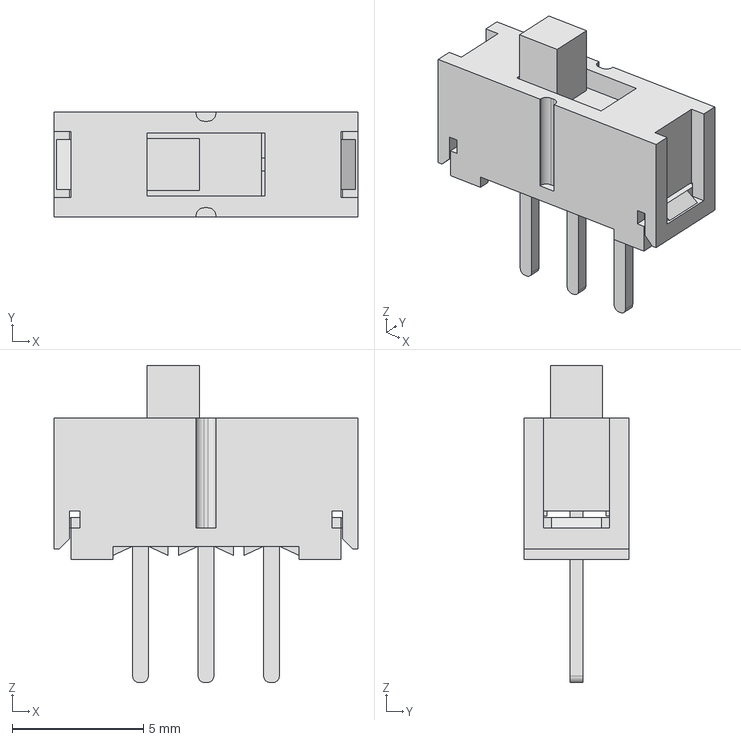
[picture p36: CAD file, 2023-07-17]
V3/electrical/design_files_KiCAD_V6 Pico/3D/SPDT_EG1218.stp
11.6 x 4.00 x 12.1 mm

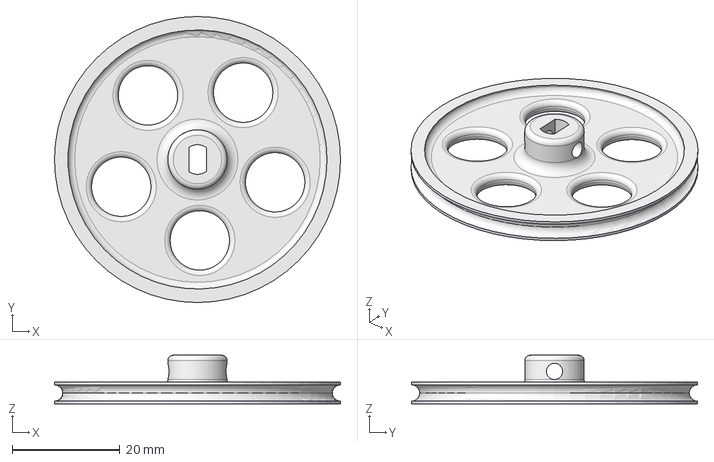
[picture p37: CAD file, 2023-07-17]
V3/mechanical/FreeCad/Wheell.FCStd
53.0 x 53.0 x 9.00 mm

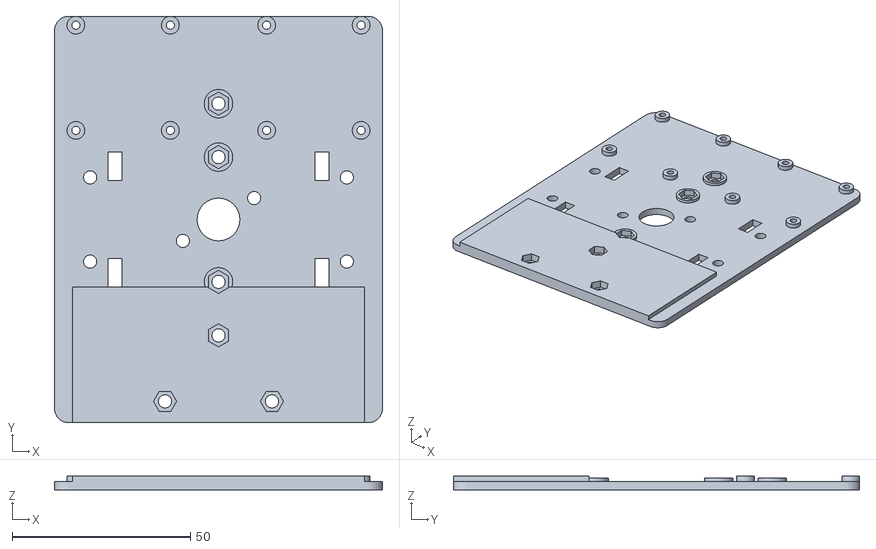
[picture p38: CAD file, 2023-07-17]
V3/mechanical/STL/Chassis_Bboard_05.stl
92.0 x 114.0 x 3.90

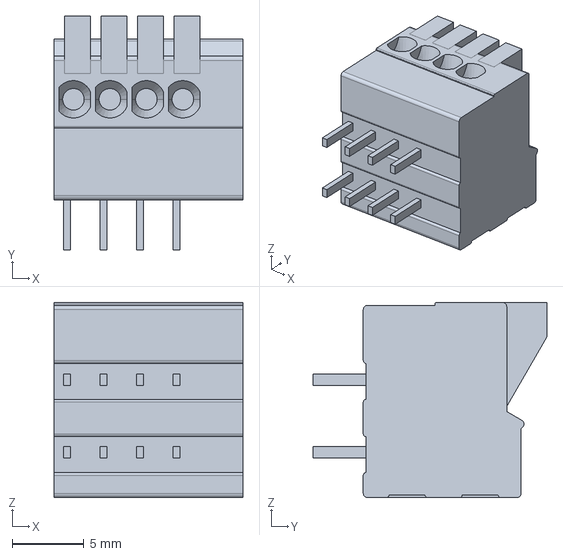
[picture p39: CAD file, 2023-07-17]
V3/electrical/design_files_KiCAD_V6 BRDBD_IR L/3D/1-2834016-4.step
13.2 x 16.3 x 13.6 mm

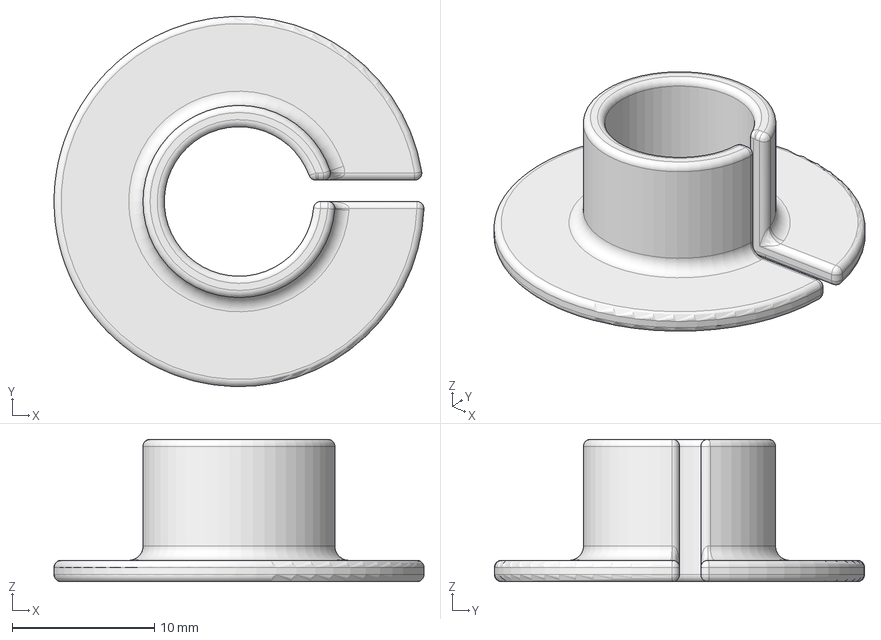
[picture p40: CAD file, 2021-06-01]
V3/mechanical/FreeCad/PenCollar.FCStd
26.0 x 26.0 x 10.0 mm

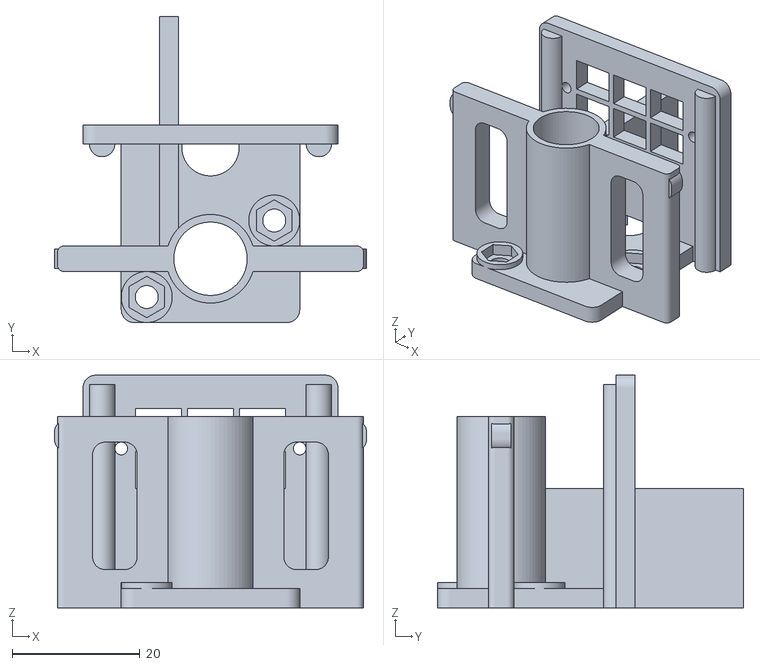
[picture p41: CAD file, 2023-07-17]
V3/mechanical/STL/Pen_Holder_04.stl
49.0 x 48.0 x 36.5

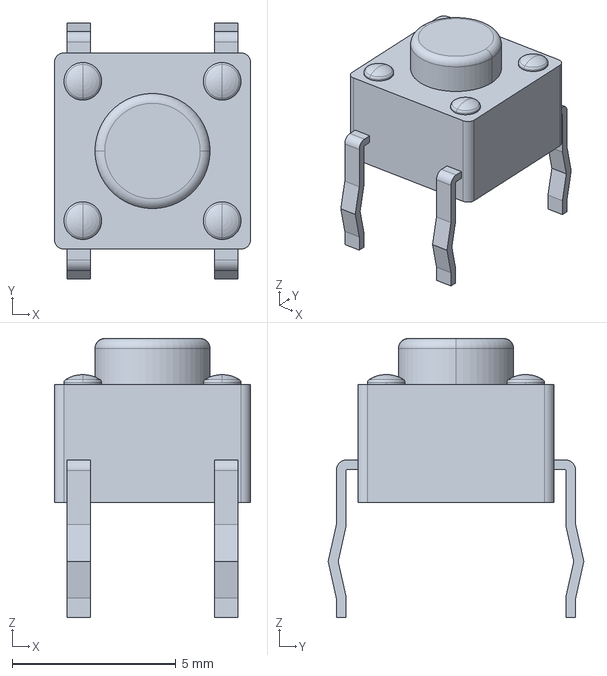
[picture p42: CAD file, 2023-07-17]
V3/electrical/design_files_KiCAD_V6 BRDBD_IR L/3D/SPST_1825910-6.stp
5.99 x 7.80 x 8.51 mm

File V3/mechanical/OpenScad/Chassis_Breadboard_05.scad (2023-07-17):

// OpenScad version 2021.01 

$fn = 32;  // smooth circles

board = "BBoard";
version = "V0.5";

baseThickness = 2.4;
railOffset = 12;     // from CL
M3holeDia = 3.7;
M3nutDia = 6.4;
holeOffset = M3holeDia * 1.2;

chassis_wid = 92;  // x   was 82
chassis_len = 114; // y  was 142
plateOffsetY = 0;  // giving up on symetry

casterOffset = 6;  // from edge

standoffDia = 7;
smallStandoffDia = 5;
standoffHeight = baseThickness + 1.5;
insertHeight = baseThickness + 1;
standoffHoleDia = 2.3; //2-28 thread forming 
holderOffsetX = 10; 
holderOffsetY = 6;

batteryOffsetY = 25;  //from CL
frontBatteryOffset = 25;
//frontBatteryOffset = backBatteryOffset + plateOffsetY - 2;
//batteryOffset = 15 + 10;  // from CL

xArduinoOffset = 17;
yArduinoOffset = -chassis_len / 2 + standoffDia / 2;

penHoleDiameter = 12.0;
penHoleRadius = penHoleDiameter / 2;

railWidth = 4;
cutout_len = 45;
cutout_wid = 15;

stepperBoardX = 26.5; // distance between mounting holes CL
stepperBoardY = 29.5;
stepperBoardXoffset = chassis_wid / 2 - stepperBoardX/2 -6; // from edge
stepperBoardYoffset = chassis_len / 2 - stepperBoardY / 2 - standoffDia + plateOffsetY+3;

itsyX = 36.5;
itsyY = 18.5; 
itsyOffsetY = 36;  //from CL
itsyOffsetX = -10;

breadBoardWidth = 82;


difference(){
    union(){ // solids
        // chassis plate
        translate([0, plateOffsetY, baseThickness/2])
        roundedCube([chassis_wid, chassis_len, baseThickness], center=true, radius=4);
            
        //itsy bitsy holder
        //translate([-itsyOffsetX, -itsyOffsetY, 0])
        //roundedCube([itsyX + 4, itsyY + 4, 6], center=true, radius=1);  

        // arduino standoffs
        //translate([xArduinoOffset, yArduinoOffset, 0]) Arduino(standoffDia);
        
        // RP2040 standoffs
         //translate([0, -chassis_len/2+plateOffsetY+9, 0]) RP2040(standoffDia);
        
        // breaboard support plates
        translate([0, -38, standoffHeight/2])
        #cube([breadBoardWidth, 38, standoffHeight], center=true);
               
        // rails
        /*
        translate([railOffset, chassis_len / 2 - (chassis_len / 2 - 15.75)/2 + plateOffsetY / 2, 0]) roundedCube(railWidth, chassis_len / 2 - 15.75 + plateOffsetY, 4, 1);

        translate([-railOffset, chassis_len / 2 - (chassis_len / 2 - 15.75)/2 + plateOffsetY / 2, 0]) roundedCube(railWidth, chassis_len / 2 - 15.75 + plateOffsetY, 4, 1);

        translate([railOffset, -chassis_len / 2 + (chassis_len / 2 - 15.75)/2 + plateOffsetY / 2 , 0]) roundedCube(railWidth, chassis_len / 2 - 15.75 - plateOffsetY, 4, 1);

        translate([-railOffset, -chassis_len / 2 + (chassis_len / 2 - 15.75)/2 + plateOffsetY / 2, 0]) roundedCube(railWidth, chassis_len / 2 - 15.75 - plateOffsetY, 4, 1);
        */    

        // stepper board standoffs
        translate([-stepperBoardXoffset, stepperBoardYoffset, 0]) stepperBoard(smallStandoffDia);
        translate([stepperBoardXoffset, stepperBoardYoffset, 0]) stepperBoard(smallStandoffDia);

        // caster standoffs
        translate([0, -(chassis_len / 2 - casterOffset  + plateOffsetY), 0])
        caster(standoffDia + 1);
        
        // battery standoffs
        translate([0, -batteryOffsetY, 0])
        battery(standoffDia + 1);
        translate([0, batteryOffsetY, 0])
        battery(standoffDia + 1);
    }


    union() { // holes
        // Arduino mount holes
        //translate([xArduinoOffset, yArduinoOffset, 0]) Arduino(standoffHoleDia);  

        // RP2040 standoffs
         //translate([0, -chassis_len/2+plateOffsetY+9, 0]) RP2040(standoffHoleDia);
        
        // stepperBoard
        translate([-stepperBoardXoffset, stepperBoardYoffset, 0]) stepperBoard(standoffHoleDia);
        translate([stepperBoardXoffset, stepperBoardYoffset, 0]) stepperBoard(standoffHoleDia);   
           
        // center pen hole
        cylinder(baseThickness, penHoleRadius, penHoleRadius); 
     
        // pen holder 
        translate([-holderOffsetX, -holderOffsetY, 0])
        cylinder(baseThickness, d=M3holeDia);     // lower left
        translate([holderOffsetX, holderOffsetY, 0])
        cylinder(baseThickness, d=M3holeDia);      // upper right
        
        // stepper bracket holes
        bracketOffset = 10;
        translate([-chassis_wid / 2 + bracketOffset, 0, 0])
        stepperBracketHoles(M3holeDia);
        translate([chassis_wid / 2 - bracketOffset, 0, 0])
        stepperBracketHoles(M3holeDia);
               
        // wire cutouts

        cutoutOffsetX = 58 / 2;         // from CL
        cutoutOffsetY = batteryOffsetY - 10; // from CL
        cutoutX = 4;
        cutoutY = 8;
        cutoutZ = 5;

        translate([-cutoutOffsetX, cutoutOffsetY, 0])
        cube([cutoutX, cutoutY, cutoutZ], center=true); 

        translate([-cutoutOffsetX, -cutoutOffsetY, 0])
        cube([cutoutX, cutoutY, cutoutZ], center=true); 
        
        translate([cutoutOffsetX, cutoutOffsetY, 0])
        cube([cutoutX, cutoutY, cutoutZ], center=true); 

        translate([cutoutOffsetX, -cutoutOffsetY, 0])
        cube([cutoutX, cutoutY, cutoutZ], center=true); 

        /*
        translate([chassis_wid / 2 - battertyCuttoutOffset - M3holeDia, -backBatteryOffset, 0])
        cube([M3holeDia, M3holeDia * 2, baseThickness, ]); 
        translate([-chassis_wid / 2 + battertyCuttoutOffset, backBatteryOffset - M3holeDia * 2, 0])
        cube([M3holeDia, M3holeDia * 2, baseThickness, ]); 
        translate([chassis_wid / 2 - battertyCuttoutOffset - M3holeDia, backBatteryOffset - M3holeDia * 2, 0])
        cube([M3holeDia, M3holeDia * 2, baseThickness, ]); 
        */

        //translate([railOffset - railWidth * 1.5, 0, 0])
        
        //cube([M3holeDia, M3holeDia * 2, baseThickness, ]); 
        
        // caster mount holse
        translate([0, -(chassis_len / 2 - casterOffset + plateOffsetY), 0])
        caster(M3holeDia);
        
        // caster nuts    
        translate([0, -(chassis_len / 2 - casterOffset + plateOffsetY), baseThickness - 1])
        caster(M3nutDia, sides=6); 
        
        // battery holes
        translate([0, -batteryOffsetY, 0])
        battery(M3holeDia);
        translate([0, batteryOffsetY, 0])
        battery(M3holeDia);
        
        // battery nuts
        translate([0, -batteryOffsetY, baseThickness - 1])
        battery(M3nutDia, sides=6);
        translate([0, batteryOffsetY, baseThickness - 1])
        battery(M3nutDia, sides=6);

        /*
        //itsy bitsyv cutouts
        translate([-itsyOffsetX, -itsyOffsetY, 4]){
            roundedCube([itsyX, itsyY, 10], radius=1, center=true);
            roundedCube([itsyX + 8, itsyY - 8, 6], radius=1, center=true);  // usb cutout
        }
        translate([-itsyOffsetX, -itsyOffsetY, 3])
        roundedCube([itsyX - 4, itsyY - 4, 10], radius=1, center=true);
        */
        
        //version cutout
        rotate([0, 180, 0])
        translate([-chassis_wid/2+3, 2, -0.3])
        linear_extrude(10)
        text(board, size = 5, font="Arial:style=Bold");
        rotate([0, 180, 0])
        translate([-chassis_wid/2+3, -6, -0.3])
        linear_extrude(10)
        text(version, size = 5, font="Arial:style=Bold");
    }
}



module battery(dia, sides=64, z=0){
    color("red"){
        if (sides==6){ // extend cut upward
            rotate([0, 0, 0])
            translate([0, 7.5, z])
            rotate([0, 0, 30])
            cylinder(10, d=dia, $fn=sides);  
            translate([0, -7.5, z])
            rotate([0, 0, 30])
            cylinder(10, d=dia, $fn=sides);
        }
        else {
            translate([0, 7.5, z])
            cylinder(insertHeight, d=dia, $fn=sides);  
            translate([0, -7.5, z])
            cylinder(insertHeight, d=dia, $fn=sides);    
        }
    }
}


module caster(dia, sides=64){
    color("darkblue"){
        translate([-15, 0, 0])
        cylinder(insertHeight, d=dia, $fn=sides);     
        translate([15, 0, 0])
        cylinder(insertHeight, d=dia, $fn=sides); 
    }
}


module stepperBoard(dia){ // centered symetrically
    translate([-stepperBoardX/2, -stepperBoardX/2, 0])
    color("blue"){ // lower left (0,0 reference)
        cylinder(standoffHeight, dia / 2, dia / 2);    
        translate([0, stepperBoardY, 0])                // upper left
        cylinder(standoffHeight, dia / 2, dia / 2);
        translate([stepperBoardX, stepperBoardY, 0])    // upper right
        cylinder(standoffHeight, dia / 2, dia / 2);
        translate([stepperBoardX, 0, 0])                // lower right
        cylinder(standoffHeight, dia / 2, dia / 2);
    }
}


module stepperBracketHoles(dia){
    translate([0, 11.8, 0])cylinder(baseThickness, d=dia); 
    translate([0, -11.8, 0])cylinder(baseThickness, d=dia); 
}


module Arduino(dia){
    color("lightblue"){
        // lower right USB (0,0 reference)
        cylinder(standoffHeight, dia / 2, dia / 2);
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

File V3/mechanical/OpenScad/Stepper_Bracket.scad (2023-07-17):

// 28byj 48 Stepper Motor Mount
// https://www.amazon.com/dp/B015RQ97W8


$fn = 64;  // smooth circles

version = "V0.1";

M3holeDia = 3.6;
M3nutDia = 6.5;
thickness = 3;
base_len = 32;   // y axis
base_wid = 21; // x axis


difference(){
    union(){ // SOLIDS
        //base plate
        translate([base_wid/2, 0, 0])
        roundedCube([base_wid, base_len, thickness], center=true);

        //bulkhead
        translate([0, 0, 22.5/2])
        rotate([0, 90, 0])
        roundedCube([22.5, 45, thickness], center=true);

        //fillet
        radius = 5;
        difference(){
            offset = thickness + radius / 2;
            translate([offset, 0, offset])
            cube([radius, base_len, radius], center=true);
            translate([offset + radius/2, 0, offset + radius / 2])
            rotate([90, 90, 0])
            cylinder(h=33, r=radius, center=true);
        }
    }

    union(){ // CUTOUTS
        //bolt holes
        translate([10, 12., 0]) cylinder(10, d=M3holeDia); 
        translate([10, -12., 0]) cylinder(10, d=M3holeDia);
        translate([10, 12., 1.5]) cylinder(10, d=M3nutDia, $fn=6); 
        translate([10, -12., 1.5]) cylinder(10, d=M3nutDia, $fn=6); 

        // stepper
        translate([14.5, 0, 15]) //14.4
        rotate([90, 0, -90])
        stepper();
    }
}


module stepper(){
    height=25;
    tab_width = 8;
    cylinder(h=height, r=14.5, center=true); // stepper body
    translate([17.5,0,0]) cylinder(h=height, r=tab_width/2, center=true); 
    translate([-17.5,0,0]) cylinder(h=height, r=tab_width/2, center=true); 
    translate([-17.5,0,5]) cylinder(h=height+10, d=M3holeDia, center=true); 
    translate([17.5,0,5]) cylinder(h=height+10, d=M3holeDia, center=true); 
    cube([35, tab_width, height], center=true);
    translate([0,-8,5])cylinder(h=height+10, r=5.5, center=true);
    translate([0,10,0]) cube([20, 17, height], center=true);
}


module roundedCube(dims, radius=2, center=false){
    // attempt at replicated cube, but with rounded edges from
    // https://youtu.be/gKOkJWiTgAY
    xdim =dims[0];
    ydim =dims[1];
    zdim =dims[2];
    
    if (center) {
        translate([-xdim/2, -ydim/2, 0]){
            hull(){ 
                translate([radius, radius, 0]) cylinder(zdim, radius, radius);
                translate([xdim-radius, radius, 0]) cylinder(zdim, radius, radius);
                translate([radius, ydim-radius, 0]) cylinder(zdim, radius, radius);
                translate([xdim-radius, ydim-radius, 0]) cylinder(zdim, radius, radius);
            }
        }
    }
    else{
        hull(){ // https://youtu.be/gKOkJWiTgAY
            translate([radius, radius, 0]) cylinder(zdim, radius, radius);
            translate([xdim-radius, radius, 0]) cylinder(zdim, radius, radius);
            translate([radius, ydim-radius, 0]) cylinder(zdim, radius, radius);
            translate([xdim-radius, ydim-radius, 0]) cylinder(zdim, radius, radius);
        }
    }
}

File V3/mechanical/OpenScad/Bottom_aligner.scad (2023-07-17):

$fn = 64;

boreDiameter = 8.8;  // pen diameter + clearance
boreRadius = boreDiameter / 2;

baseThickness = 3;
M3holeDia = 3.6;
M3nutDia = 6.6;
baseLen = 18;
baseWid = 28;

barrelHieght = 12;
barrelWallThickness = 1.2;

standoffDia = 8;
standoffThickness = 3;
holderOffsetX = 10;
holderOffsetY = -6;


// PEN HOLDER

difference(){
    //solids
    union(){
        // base
        roundedCube([baseWid, baseLen, baseThickness], center=true, radius=2);

        // barrel
        cylinder(	barrelHieght, r1=boreRadius + barrelWallThickness, 
                    r2=boreRadius + barrelWallThickness );
        
        // standoffs
        //translate([holderOffsetX, holderOffsetY, 0])
        //cylinder( standoffThickness, d=standoffDia);
        //translate([-holderOffsetX, -holderOffsetY, 0])
        //cylinder( standoffThickness, d=standoffDia);        
    }

    //cutouts
    union(){
        // bore
        cylinder(barrelHieght + 1, boreRadius, boreRadius);        
        
        //mount holes
        hole_offset = 5;
        translate([holderOffsetX, holderOffsetY, 0])
        cylinder( baseThickness, d=M3holeDia);
        translate([holderOffsetX, holderOffsetY, 2])  rotate([0,0,90])      
        cylinder( baseThickness * 2, d=M3nutDia);        

        translate([-holderOffsetX,- holderOffsetY, 0])
        cylinder( baseThickness, d=M3holeDia);   
        translate([-holderOffsetX, -holderOffsetY, 2]) rotate([0,0,90])
        cylinder( baseThickness * 2, d=M3nutDia);


    }
}





module roundedCube(dims, radius=2, center=false){
    // attempt at replicated cube, but with rounded edges from
    // https://youtu.be/gKOkJWiTgAY
    xdim =dims[0];
    ydim =dims[1];
    zdim =dims[2];
    
    if (center) {
        translate([-xdim/2, -ydim/2, 0]){
            hull(){ 
                translate([radius, radius, 0]) cylinder(zdim, radius, radius);
                translate([xdim-radius, radius, 0]) cylinder(zdim, radius, radius);
                translate([radius, ydim-radius, 0]) cylinder(zdim, radius, radius);
                translate([xdim-radius, ydim-radius, 0]) cylinder(zdim, radius, radius);
            }
        }
    }
    else{
        hull(){ // https://youtu.be/gKOkJWiTgAY
            translate([radius, radius, 0]) cylinder(zdim, radius, radius);
            translate([xdim-radius, radius, 0]) cylinder(zdim, radius, radius);
            translate([radius, ydim-radius, 0]) cylinder(zdim, radius, radius);
            translate([xdim-radius, ydim-radius, 0]) cylinder(zdim, radius, radius);
        }
    }
}


module OldroundedCube(xdim ,ydim ,zdim, rdim){
    translate([-xdim/2, -ydim/2, 0])
	hull(){ // https://youtu.be/gKOkJWiTgAY
		translate([rdim, rdim, 0]) cylinder(zdim, rdim, rdim);
		translate([xdim-rdim, rdim, 0]) cylinder(zdim, rdim, rdim);
		translate([rdim, ydim-rdim, 0]) cylinder(zdim, rdim, rdim);
		translate([xdim-rdim, ydim-rdim, 0]) cylinder(zdim, rdim, rdim);
	}
}

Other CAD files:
V3/electrical/design_files_KiCAD_V6 BRDBD_IR R/BRBD_IR.obj
V3/electrical/design_files_KiCAD_V6 BRDBD_IR L/BRBD_IR.obj
V3/electrical/design_files_KiCAD_V6 BRDBD_PWR/project.step
V3/mechanical/OpenScad/Pen_Holder_04.scad
V1/mechanical/FreeCad/Nameplate.FCStd
V1/mechanical/FreeCad/penCollar.FCStd
V1/mechanical/FreeCad/stepperMount_v01.FCStd
V1/mechanical/FreeCad/wheel.FCStd
V1/mechanical/FreeCad/wheel_v01.FCStd
V1/mechanical/OpenSCAD/Caster.scad
V1/mechanical/OpenSCAD/Chassis.scad
V1/mechanical/OpenSCAD/Chassis_MicroBit.scad
V1/mechanical/OpenSCAD/Chassis_MicroBit.stl
V1/mechanical/OpenSCAD/Chassis_Tinsy_V0.scad
V1/mechanical/OpenSCAD/Chassis_V01.scad
V1/mechanical/OpenSCAD/Chassis_V02.scad
V1/mechanical/OpenSCAD/Pen_Collar.scad
V1/mechanical/OpenSCAD/Pen_Collar_10-5.scad
V1/mechanical/OpenSCAD/Pen_Holder.scad
V1/mechanical/OpenSCAD/Pen_Holder_V01.scad
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

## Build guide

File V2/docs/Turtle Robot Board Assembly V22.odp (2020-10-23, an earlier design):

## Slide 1

1. Resistors:

- No polarity
- 330 ohm = orange-orange-brown-gold
- 10K ohm = brown-black-orange-gold

Turtle Robot Board Assembly (V2.2)

Assemble in order indicated.

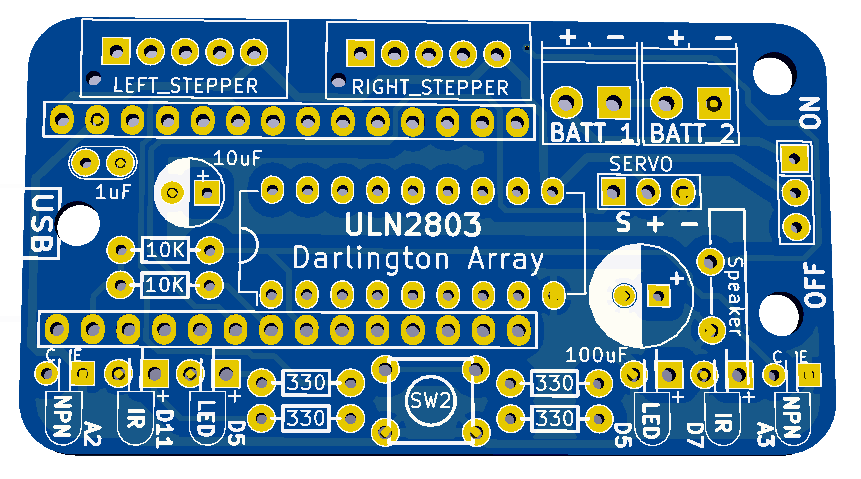
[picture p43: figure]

2. IC socket:

- Match divot on left side.
- Insert chip after Step 8.

3. Button:

- Match legs to holes
- Press to snap in place

4. LEDS / IR / Detector:

- Long leg in square pad.
- Bend leads so they face edge of board.
- Outter: Black IR NPN Detectors(A2, A3)
- Inner: Colored LEDs (D5)
- Middle: Clear IR Emitters (D7, D11)

5. Capacitors:

- 1 uF no polarity “104”
- 10 uF long leg positive, square pad.
- 100 uF long leg positive, square pad.

6.Switch: No polarity

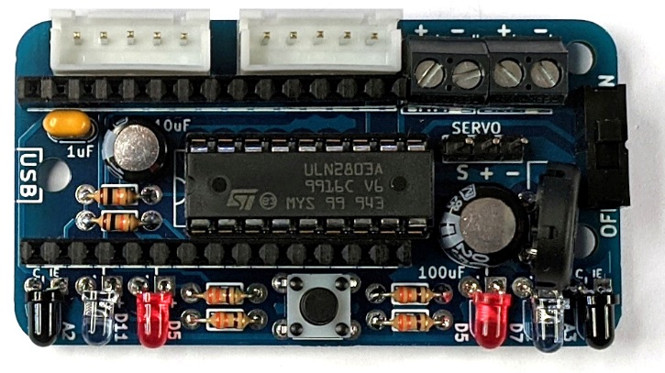
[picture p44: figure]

7. Headers:

- White JST: Slots to edge.
- Black 2-position: Openings to edge.
- Servo 3-position: long legs up

8. Speaker: No polarity.

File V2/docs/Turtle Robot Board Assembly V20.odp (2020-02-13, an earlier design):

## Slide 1

1. Resistors:

- No polarity
- 100 ohm = brown-black-brown-gold
- 330 ohm = orange-orange-brown-gold
- 10K ohm = brown-black-orange-gold

Turtle Robot Board Assembly (V2)

Assemble in order indicated.

7. Headers:

- White JST: Slots outward
- Black 2-position: Openings outward
- Servo 3-position: long legs up

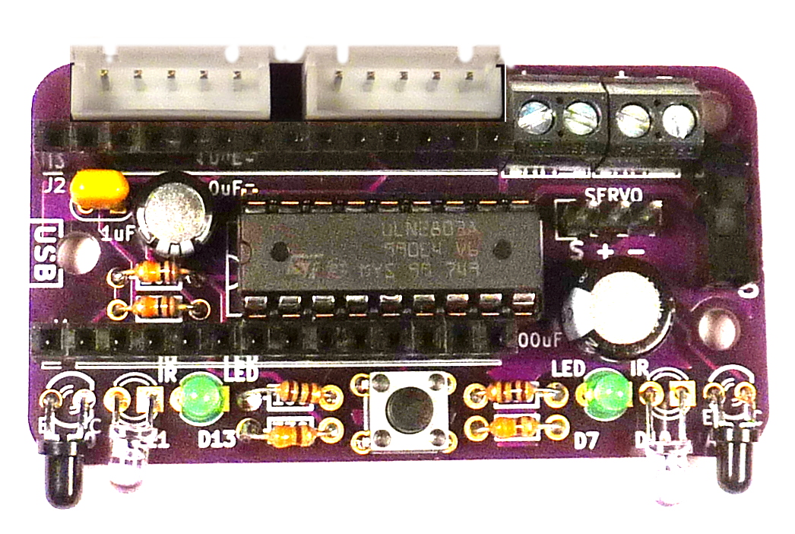
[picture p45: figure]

4. LEDS / IR / Detector:

- LED (D13, D7): long leg is positive. Square Pad
- Bend IR emitter & detector so they face the front:
  - Clear IR Emitter (D11, D10): long leg is positive. Square Pad
  - Black IR Detector (A0, A1): Long leg emmiter (“E”).

2. IC socket:

- Match divot on left side.
- Insert chip after Step 7.

6.Switch:

- No polarity

3. Button:

- Match legs to holes
- Press to snap in place

5. Capacitors:

- 1 uF no polarity “104”
- 10 uF long leg positive
- 100 uF long leg positive

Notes: <number>

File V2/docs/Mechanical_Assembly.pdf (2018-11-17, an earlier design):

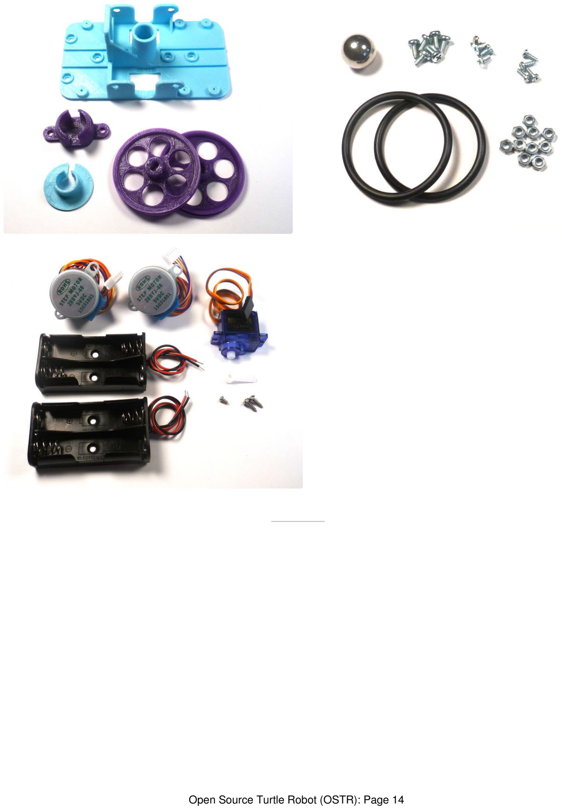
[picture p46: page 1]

Open Source Turtle Robot (OSTR): Page 14

### Step 12: ME: Chassis Prep

A "chassis" is the fame of a motor vehicle or other wheeled conveyance, and in this case the robot's chassis forms the platform for the electronics, motors, and servos.

Time to get familiar with your hardware. We will be using three different types of Phillips screws you will have to be able to identify:

Pan Head Screw (M3 x 6 mm) -> Stepper motors to Chassis Flat Head Screw (M3 x 6 mm) -> Battery Holders to Chassis Round Head Thread-Forming Screw (#2 x 1/4") -> PCB to Chassis

In order to attach parts, we are going to embed M3 nuts into the chassis.

Use an M3 round-head screw and tighten it to pull the nut into the pocket so it is seated flush. Remove the screw.

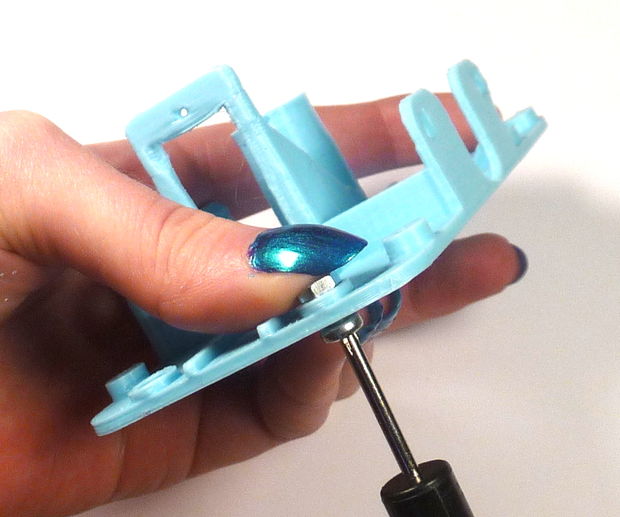
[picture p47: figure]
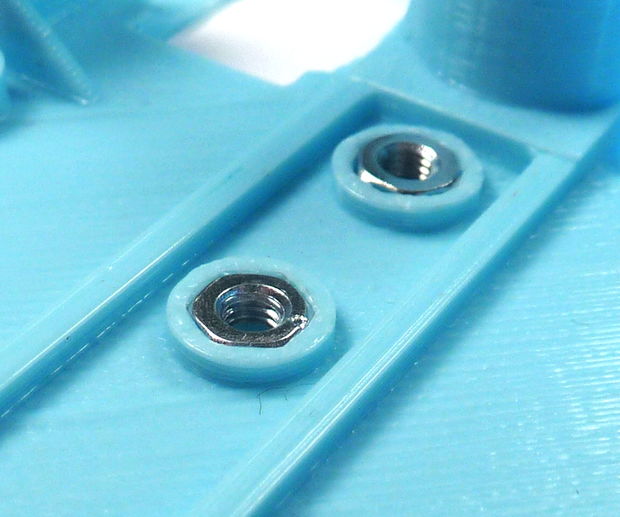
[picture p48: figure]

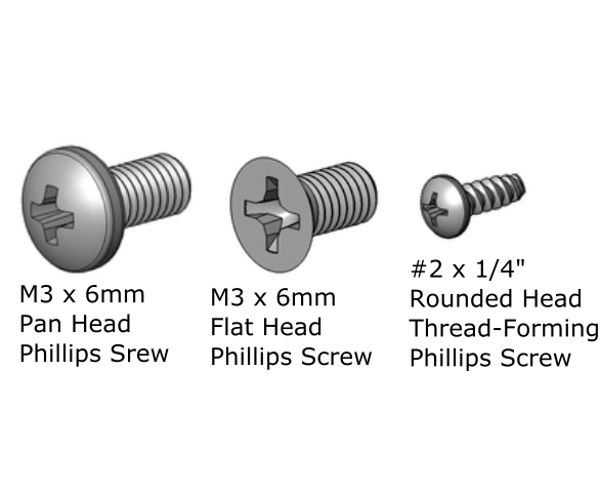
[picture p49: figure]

### Step 13: ME: Batteries

Integrating the electrical components like motors and batteries with the chassis will fall into the ME's domain.

Attach the battery holders using two M3 flat-head screws and thread the wires through the openings under the motor mounts.

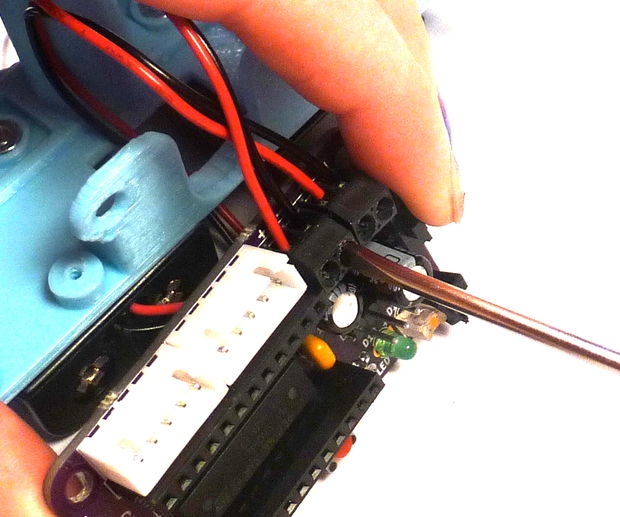
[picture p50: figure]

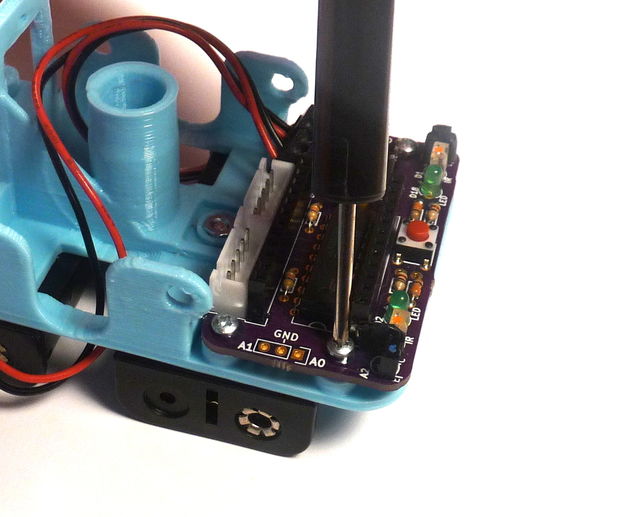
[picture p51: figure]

Put on your "EE" hat and attach the positive and negative wires to the terminals marked "+" and "-", one set of batteries for each terminal.

Attach the circuit board to the chassis using #2x1/4 thread-forming screws.
If the screws wont start, remove the PCB and use the tip of the screw driver to open them up a bit.

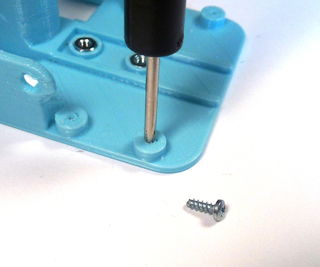
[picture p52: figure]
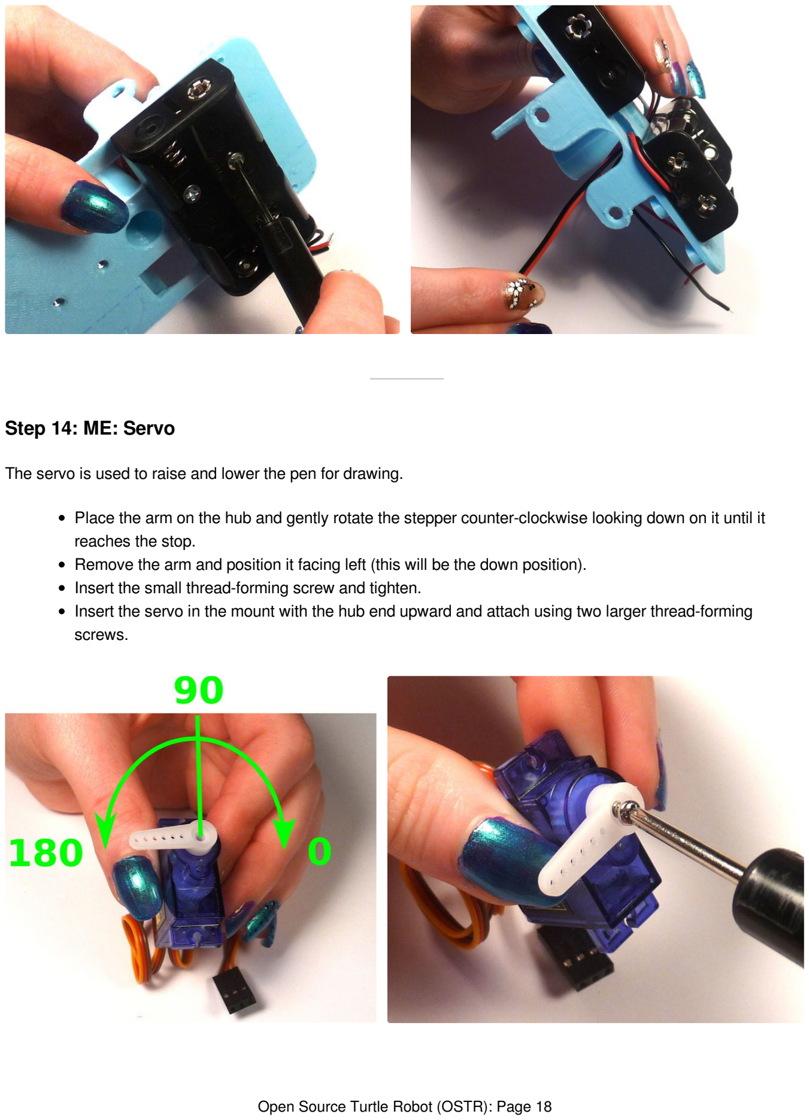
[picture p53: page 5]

### Step 14: ME: Servo

The servo is used to raise and lower the pen for drawing.

Place the arm on the hub and gently rotate the stepper counter-clockwise looking down on it until it reaches the stop.
Remove the arm and position it facing left (this will be the down position).
Insert the small thread-forming screw and tighten.
Insert the servo in the mount with the hub end upward and attach using two larger thread-forming screws.

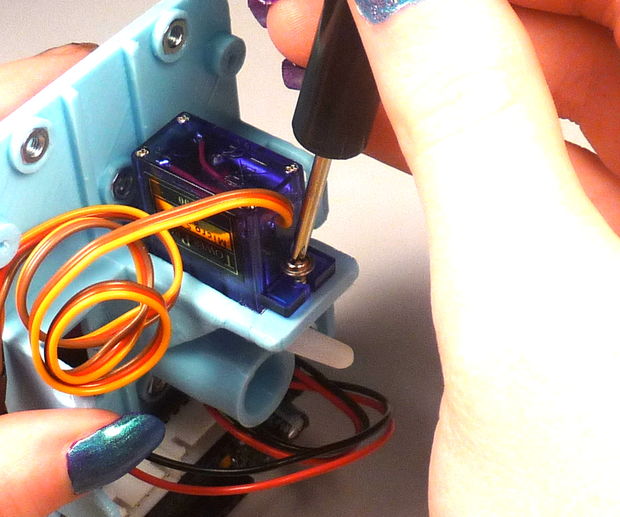
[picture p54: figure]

### Step 15: ME: Stepper Motors

Before we mount the stepper motors, check the fit of the wheels on the shaft. These should slid on fairly tightly if your printer is calibrated correctly.

If they are too tight, use a jewelers file to open up clearance. You can also heat the hub with a hair drier, but do so sparingly to avoid warping the rim.
If they are too loose, you can use an M3 round-head screw to hold the wheel to the shaft (after the motor is mounted).

We are going to pass the wires of the stepper (and servo) under the body to help with wire management.

Start with the left side and thread the wires for the stepper (and servo) through the opening with wires coming from the stepper following down the back side.
Insert the motor into the mount and attach with two M3 round-head screws and nuts.
Gently pull the wires through.

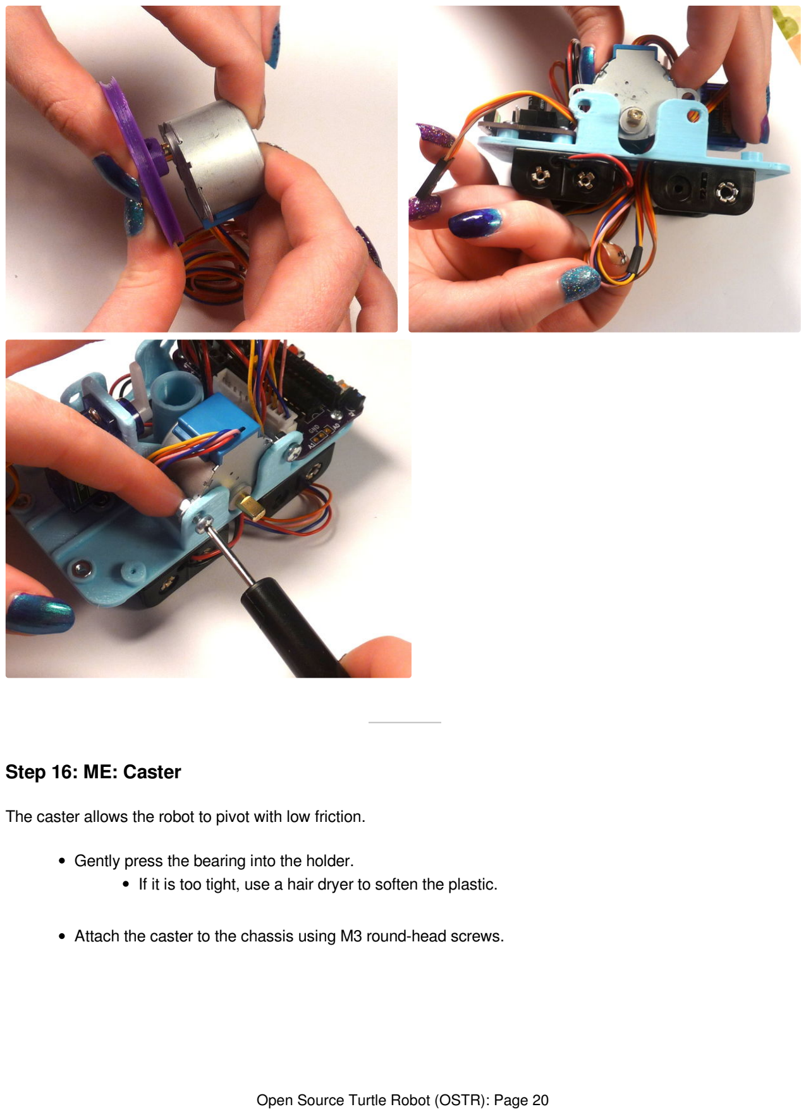
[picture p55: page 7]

### Step 16: ME: Caster

The caster allows the robot to pivot with low friction.

Gently press the bearing into the holder.
If it is too tight, use a hair dryer to soften the plastic.

Attach the caster to the chassis using M3 round-head screws.

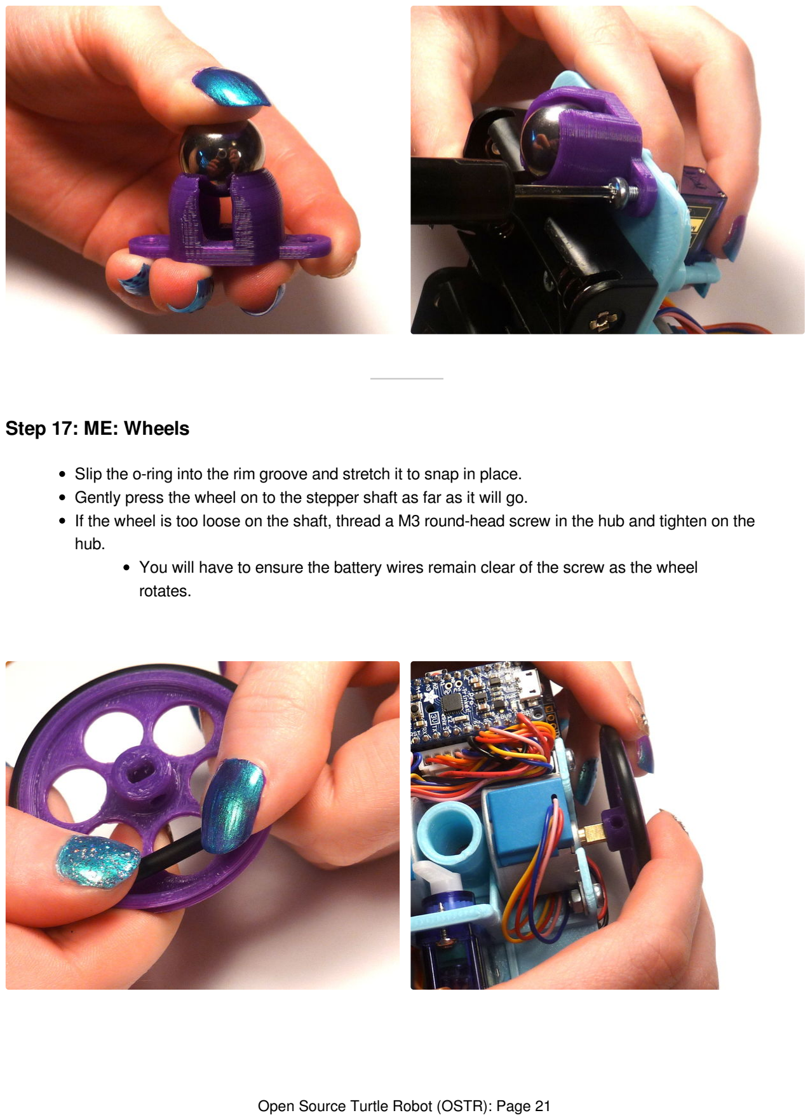
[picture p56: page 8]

### Step 17: ME: Wheels

Slip the o-ring into the rim groove and stretch it to snap in place.
Gently press the wheel on to the stepper shaft as far as it will go.
If the wheel is too loose on the shaft, thread a M3 round-head screw in the hub and tighten on the hub.
You will have to ensure the battery wires remain clear of the screw as the wheel rotates.

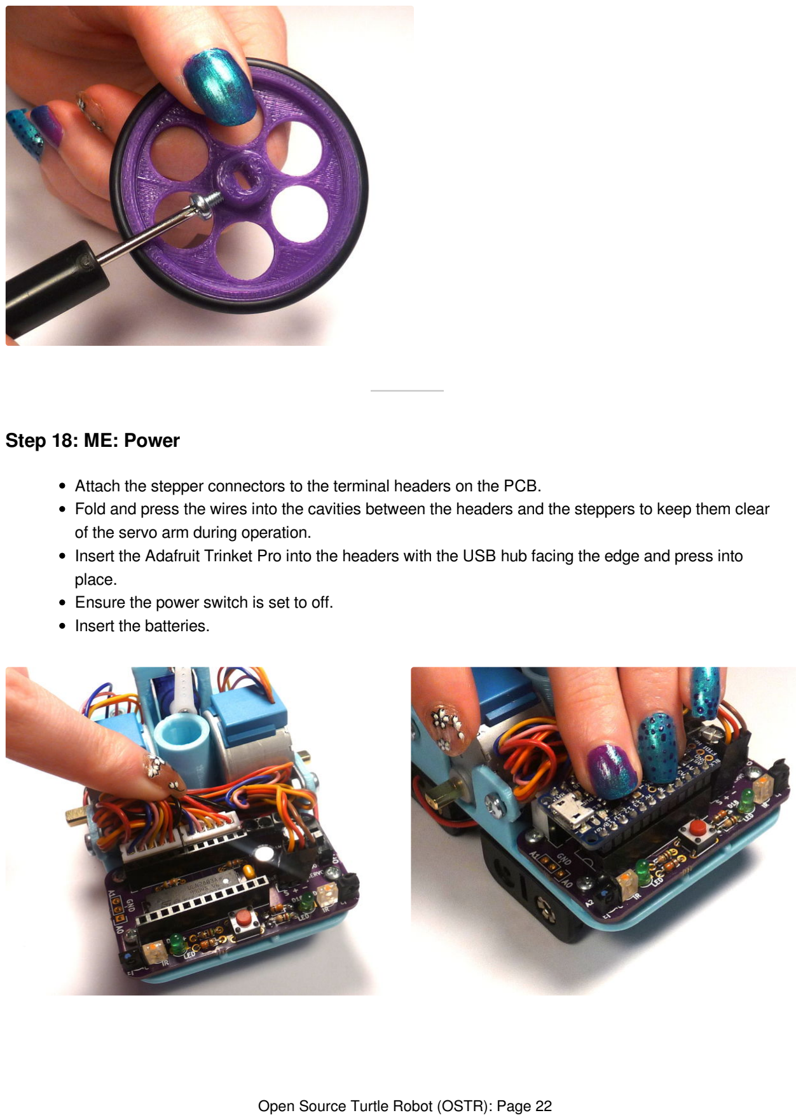
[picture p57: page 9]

### Step 18: ME: Power

Attach the stepper connectors to the terminal headers on the PCB.
Fold and press the wires into the cavities between the headers and the steppers to keep them clear of the servo arm during operation.
Insert the Adafruit Trinket Pro into the headers with the USB hub facing the edge and press into place.
Ensure the power switch is set to off.
Insert the batteries.

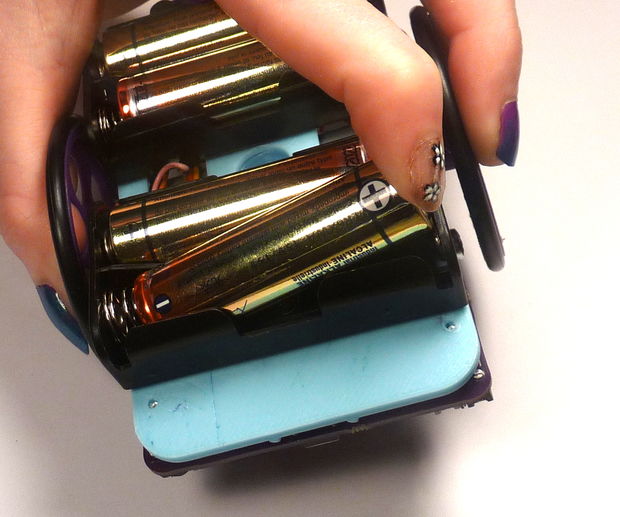
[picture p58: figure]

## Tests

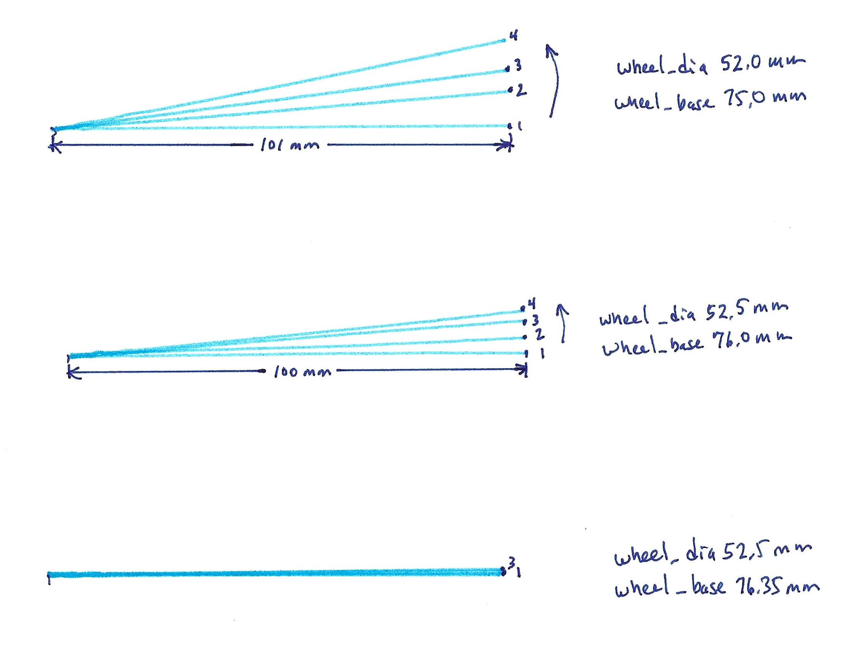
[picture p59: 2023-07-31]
V3/images/calibration.jpg

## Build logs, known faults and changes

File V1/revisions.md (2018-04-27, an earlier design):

Date		Rev		Change
4-24-18		0.0		Initial Release.
4-25-18		0.1		Thicker stepper mounts, stiffer chassis.
4-26-18		0.2		Smaller nameplate to avoid servo interference, moved chassis mounts.

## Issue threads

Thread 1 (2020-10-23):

Speaker in BOM

larsbrinkhoff, 2020-10-23:
Hello,

I don't see the speaker in the V2 BOM.

aspro648, 2020-10-23:
Sorry Lars, that is my mistake.  It didn't make it into the kit either.
I'll get one in the mail to you.

It is - 1 ea. Piezo speaker, [TDK PS1240P02CT3](
https://www.digikey.com/short/zndnmn)

*Ken Olsen*
648.ken@gmail.com | www.MakersBox.us <http://www.makersbox.us/>
<http://www.facebook.com/648.ken>  <http://linkedin.com/in/olsenken>

On Fri, Oct 23, 2020 at 10:08 AM Lars Brinkhoff <notifications@github.com>
wrote:

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

larsbrinkhoff, 2020-10-23:
Thanks!

larsbrinkhoff, 2020-10-24:
Updated BOM seems fine.

PS. Being a fan of the PDP families of computers, it was a thrill seeing our name!

Closed 2020-10-24.

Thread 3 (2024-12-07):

How to use v3

uecken, 2024-12-07:
Hi, thank you for publishing wonderful project.

Im interested in this project and would like to use  v3.
Can I use v3 by printing 3D model and making pcb board?

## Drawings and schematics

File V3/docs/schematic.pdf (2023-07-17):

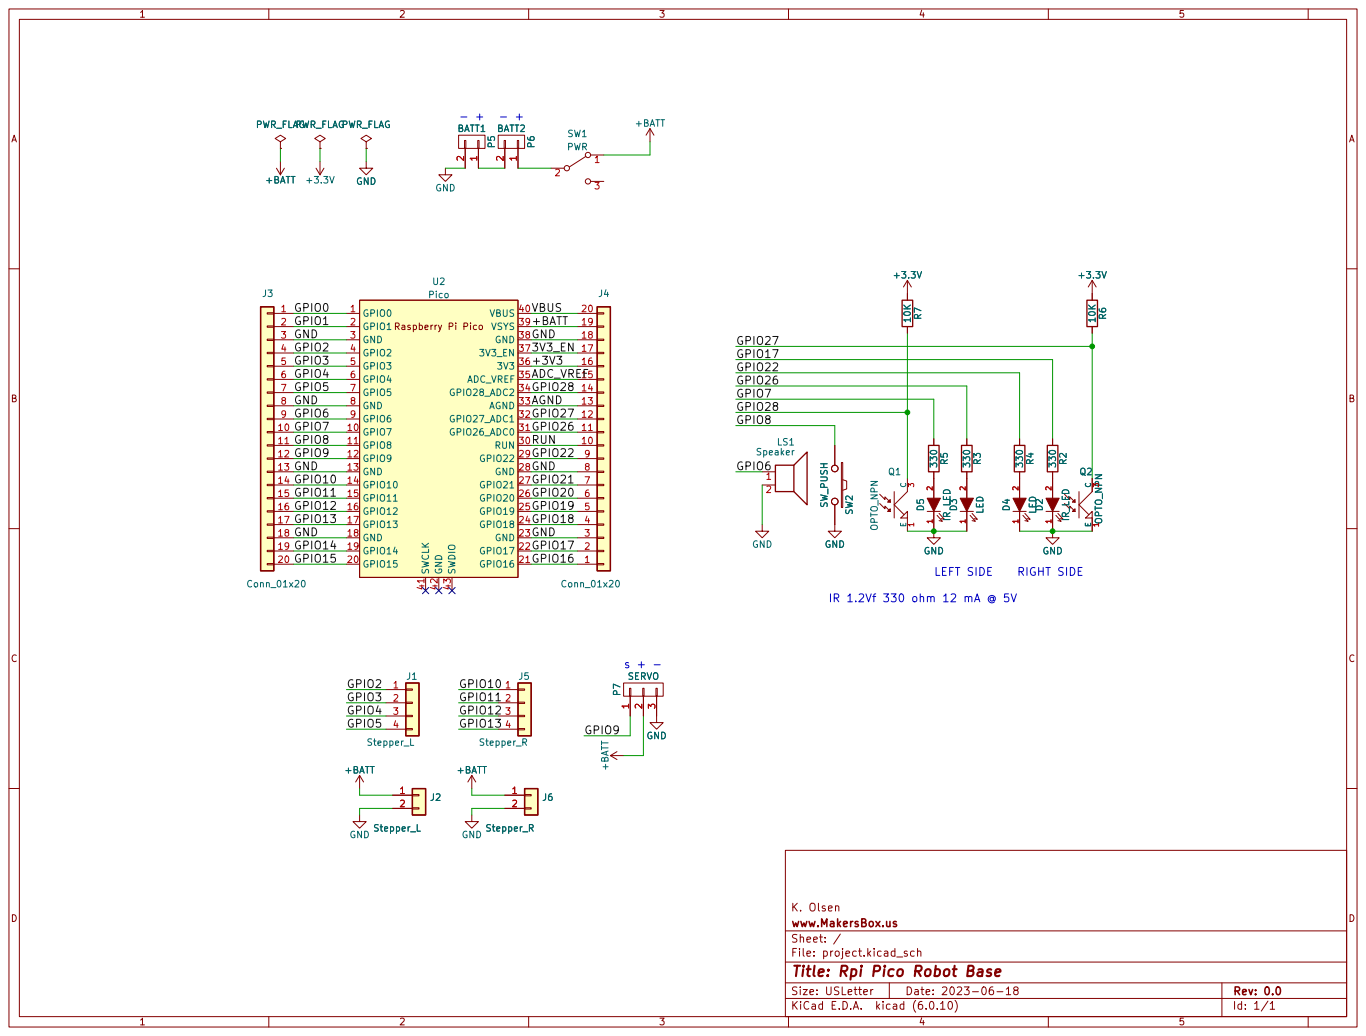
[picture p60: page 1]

2 GPIO1 | | 19
GND 3 | GND 18
4 GPIO2 | 3V3_EN | 17
GPIO7 10 | | +3V3 GPIO16 | 11

GND 8 | AGND 13
9 GPIO6 | | GPIO27 | 12
11 GPIO8 | | GPIO26 RUN GPIO21 10

12 GPIO9 | | | 9
GND 13 | | GND 8
14 GPIO10 | | | 7
GPIO11 15 | | GPIO20 | 6
16 GPIO12 | | GPIO19 | 5
17 GPIO13 | | GPIO18 | 4
GND 18 | | GND 3
19 GPIO14 | | GPIO17 | 2
GPIO15 20 | | | 1

Id: 1/1 Title: Rpi Pico Robot Base

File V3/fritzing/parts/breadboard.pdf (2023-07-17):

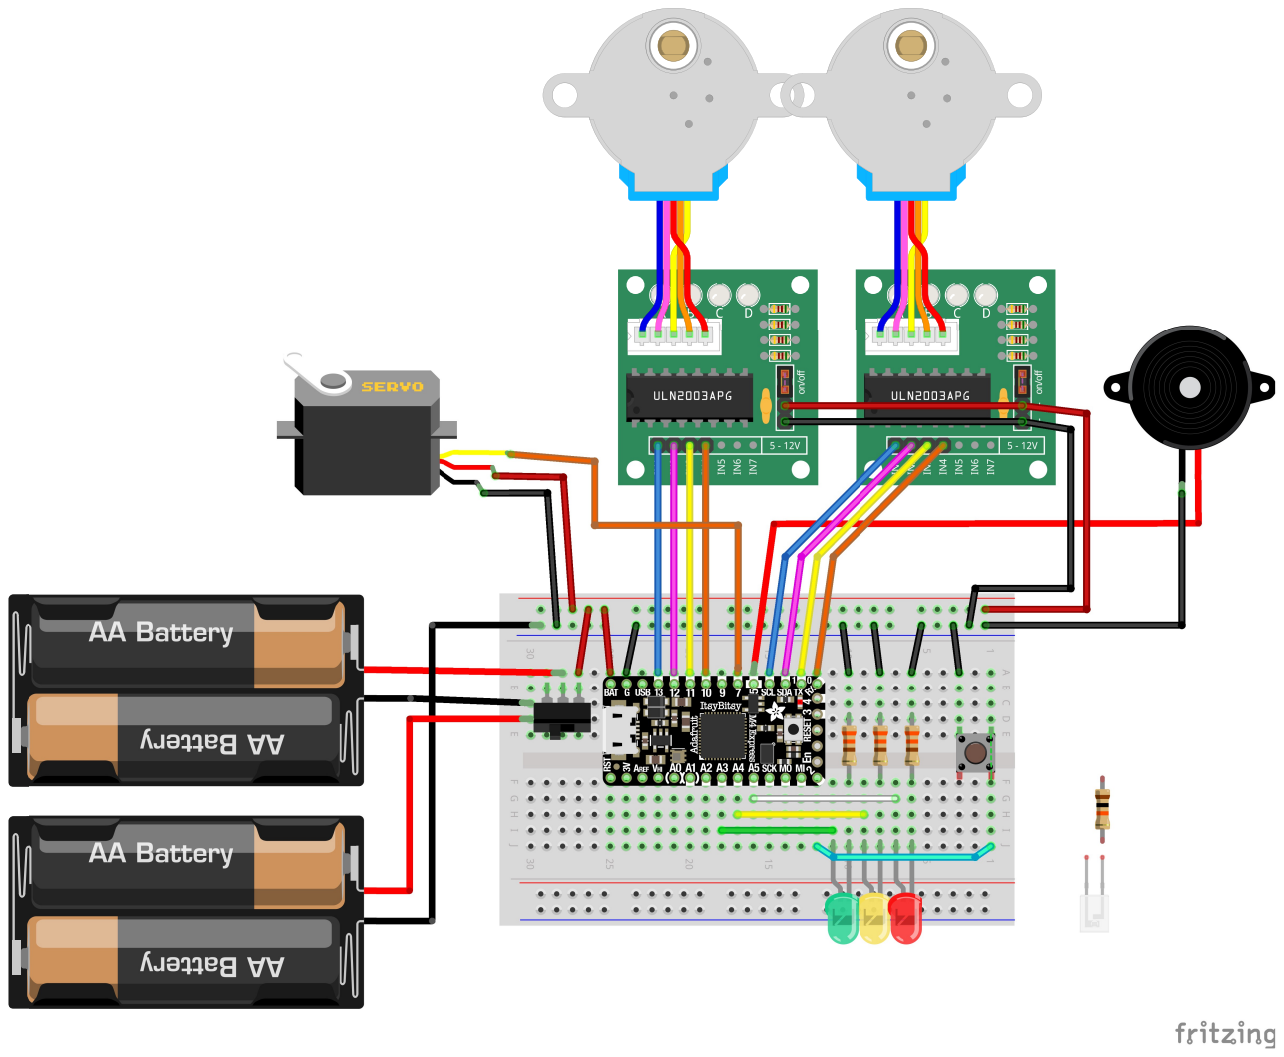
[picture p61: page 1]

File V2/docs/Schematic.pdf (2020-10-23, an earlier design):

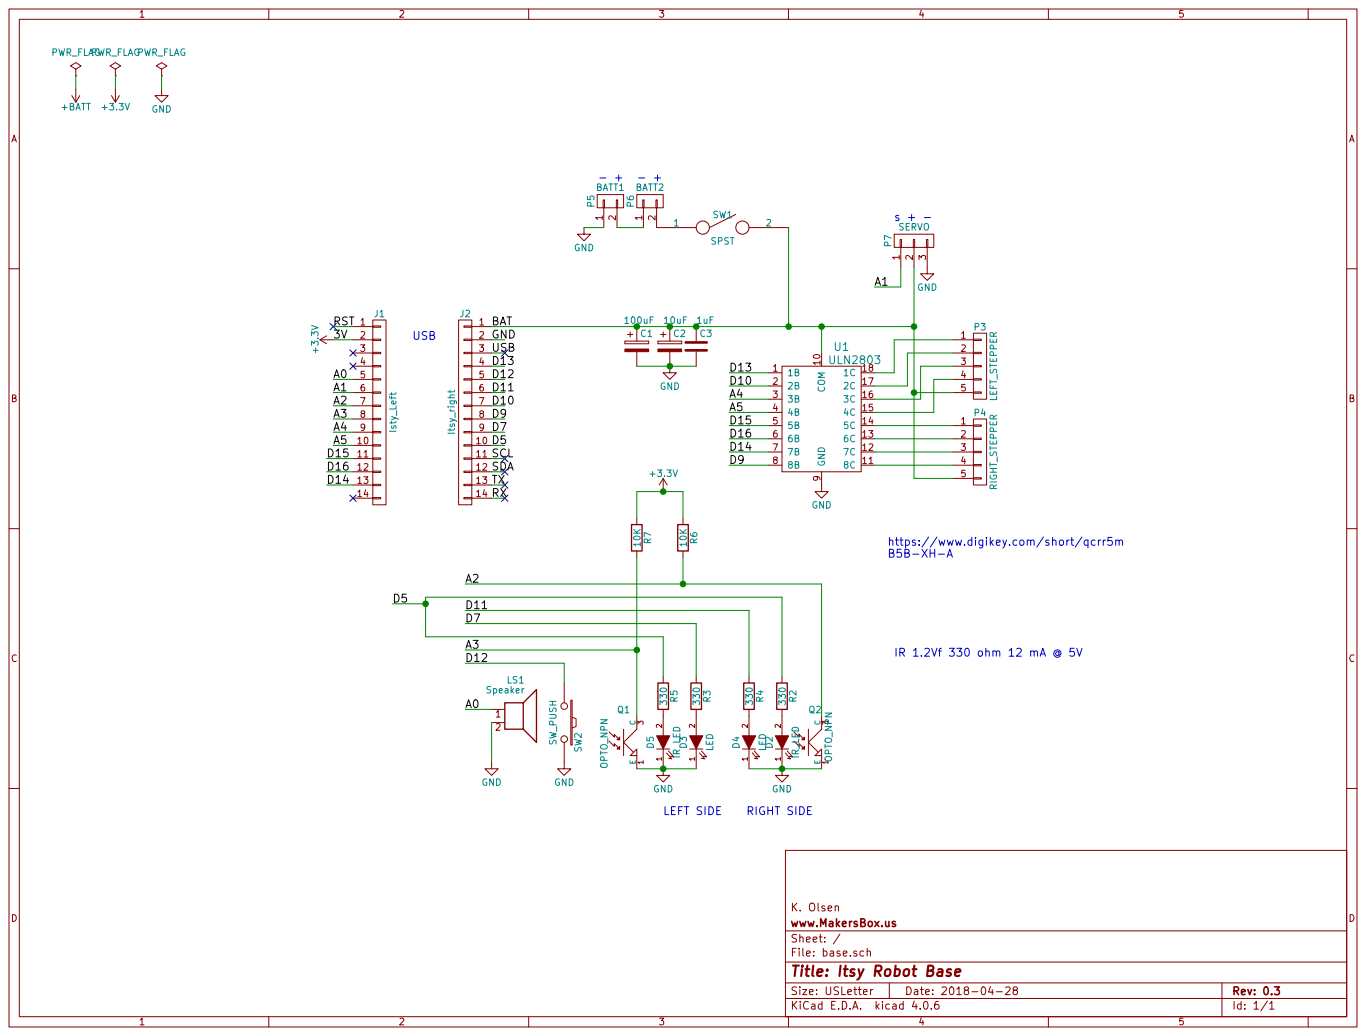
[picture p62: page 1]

https://www.digikey.com/short/qcrr5m

File: base.sch Sheet: / www.MakersBox.us K. Olsen

Id: 1/1 Title: Itsy Robot Base

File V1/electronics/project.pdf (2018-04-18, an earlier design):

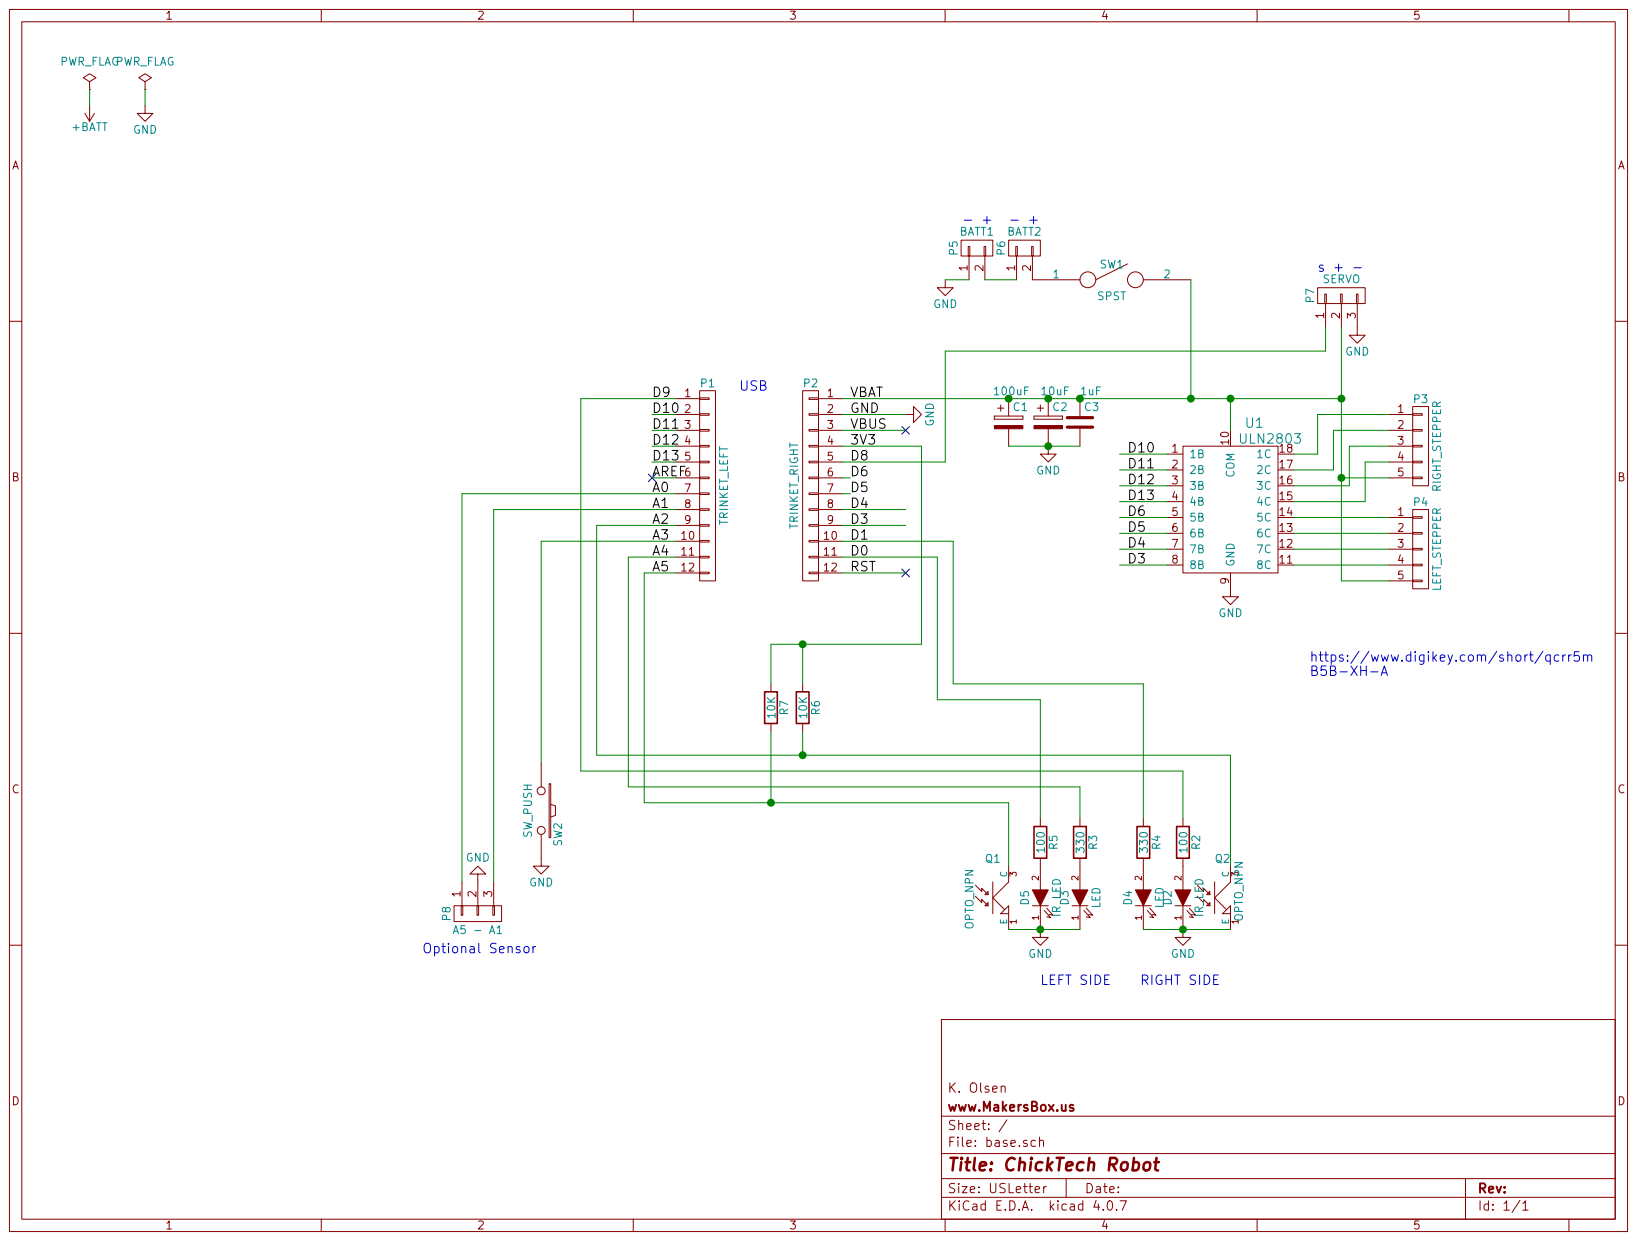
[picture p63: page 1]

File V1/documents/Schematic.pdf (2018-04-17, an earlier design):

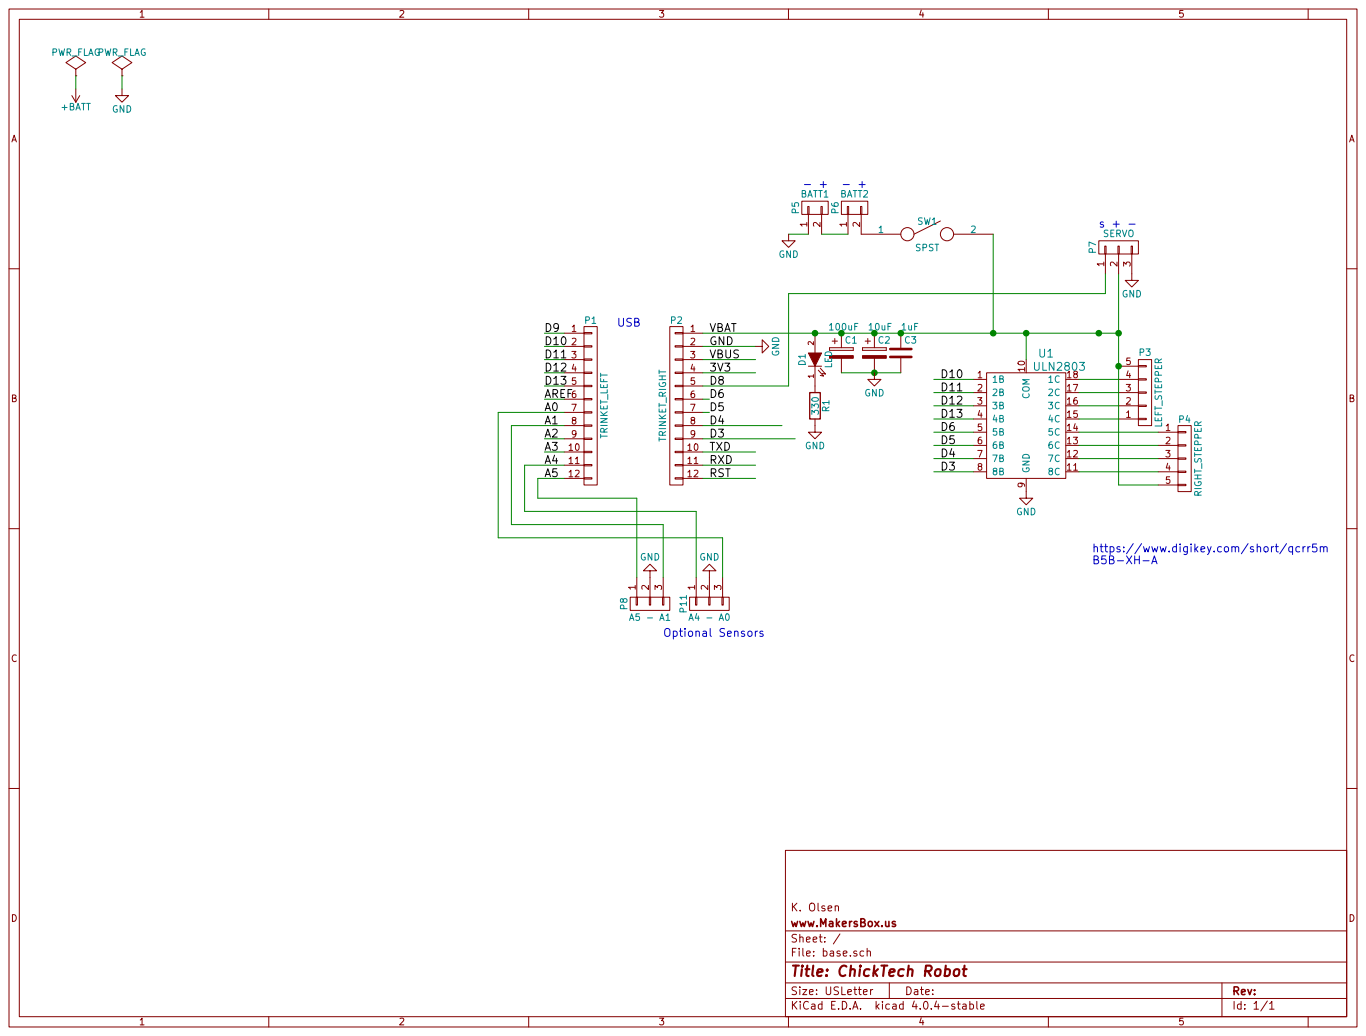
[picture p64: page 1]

https://www.digikey.com/short/qcrr5m

Id: 1/1 Title: ChickTech Robot File: base.sch Sheet: / www.MakersBox.us K. Olsen

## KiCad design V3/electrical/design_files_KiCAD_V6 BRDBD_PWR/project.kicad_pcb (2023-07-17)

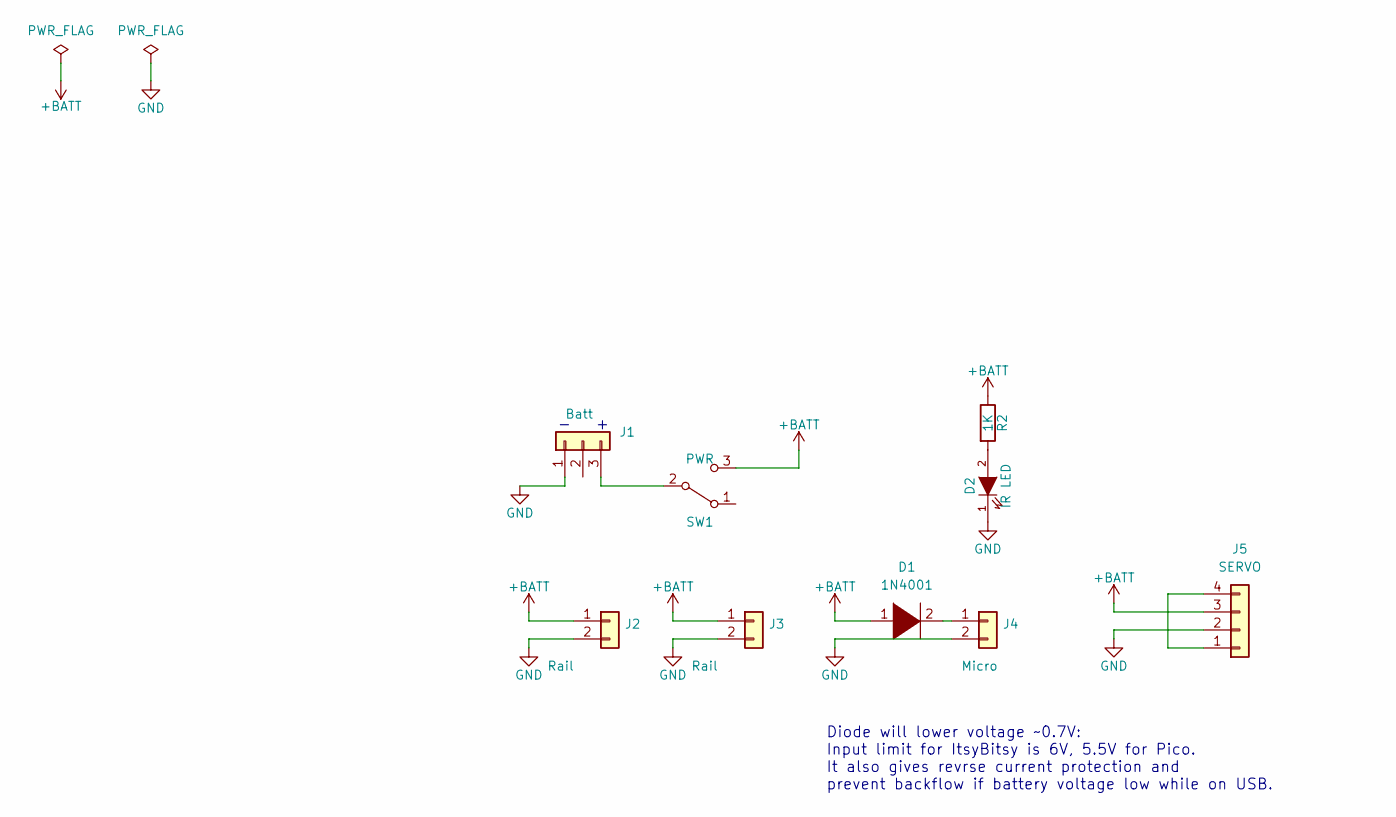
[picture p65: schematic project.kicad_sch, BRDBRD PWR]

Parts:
D1: 1N4001; D_DO-34_SOD68_P7.62mm_Horizontal
D2: IR LED; LED_D3.0mm
J1: Batt; TerminalBlock_Phoenix_PT-1,5-3-3.5-H_1x03_P3.50mm_Horizontal
J2, J3: Rail; PinHeader_1x02_P2.54mm_Vertical
J4: Micro; PinHeader_1x02_P2.54mm_Vertical
J5: SERVO; PinHeader_1x04_P2.54mm_Vertical
R2: 1K; Resistor_Horz
SW1: PWR; SW_Micro_SPST

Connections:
+BATT: D1.1 (K), J2.1, J3.1, J5.3, R2.1, SW1.3 (C)
GND: D2.1 (K), J1.1, J2.2, J3.2, J4.2, J5.2
unnamed: D2.2 (A), R2.2
unnamed: J1.3, SW1.2 (B)
unnamed: D1.2 (A), J4.1
unnamed: J5.1, J5.4

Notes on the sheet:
Diode will lower voltage ~0.7V: Input limit for ItsyBitsy is 6V, 5.5V for Pico. It also gives revrse current protection and prevent backflow if battery voltage low while on USB.
- +

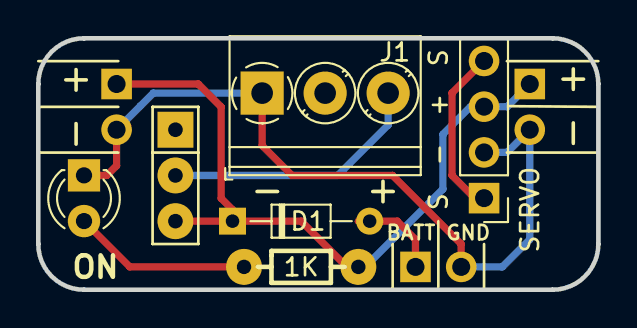
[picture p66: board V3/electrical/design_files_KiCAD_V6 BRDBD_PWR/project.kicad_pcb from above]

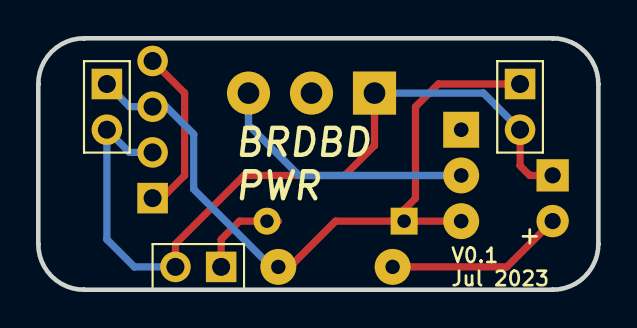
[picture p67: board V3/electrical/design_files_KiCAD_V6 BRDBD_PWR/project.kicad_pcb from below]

Board: 2 copper layers, 31.1 x 14.0 mm, 9 parts (3 on the bottom side), 6 nets.

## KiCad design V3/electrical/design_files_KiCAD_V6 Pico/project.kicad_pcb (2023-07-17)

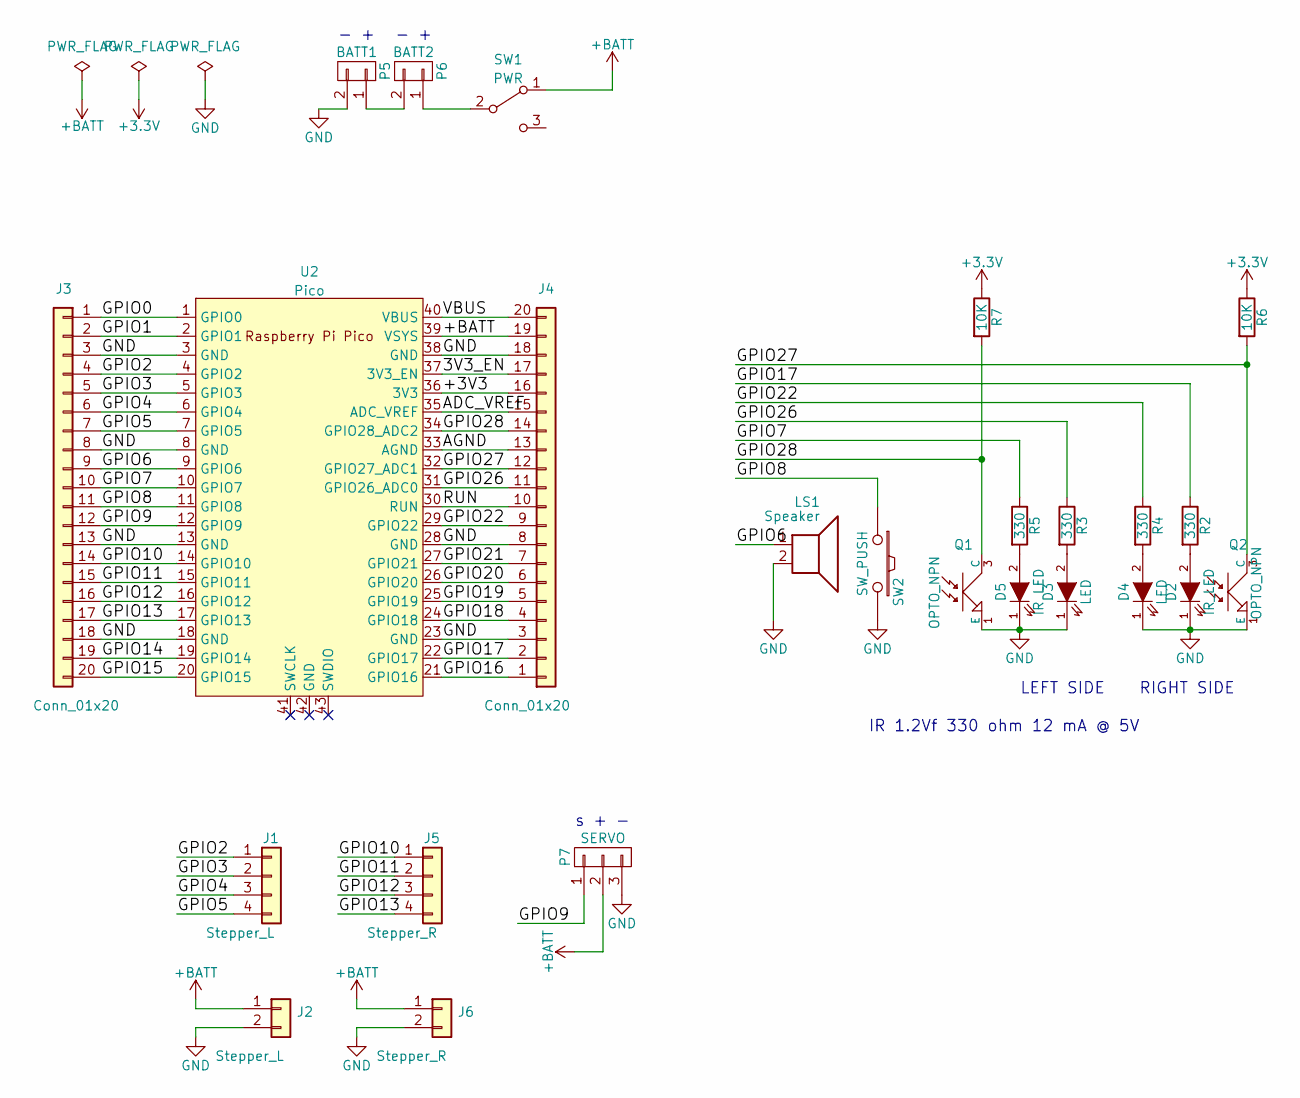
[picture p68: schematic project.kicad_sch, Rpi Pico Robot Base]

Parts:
D2: IR_LED; LED-3MM_RA
D3, D4: LED; LED-3MM_RA
D5: IR LED; LED-3MM_RA
J1: Stepper_L; PinHeader_1x04_P2.54mm_Vertical
J2: Stepper_L; PinHeader_1x02_P2.54mm_Vertical
J3, J4: Conn_01x20; PinHeader_1x20_P2.54mm_Vertical
J5: Stepper_R; PinHeader_1x04_P2.54mm_Vertical
J6: Stepper_R; PinHeader_1x02_P2.54mm_Vertical
LS1: Speaker; PS1240_piezo
P5: BATT1; TerminalBlock_Pheonix_PT-3.5mm_2pol
P6: BATT2; TerminalBlock_Pheonix_PT-3.5mm_2pol
P7: SERVO; Pin_Header_Straight_1x03
Q1, Q2: OPTO_NPN; PHOTOTRANS-RA
R2, R3, R4, R5: 330; Resistor_Horz
R6, R7: 10K; Resistor_Horz
SW1: PWR; SW_Micro_SPST
SW2: SW_PUSH; SW_PUSH_SMALL
U2: Pico; RPi_Pico_SMD_TH

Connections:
+BATT: J2.1, J4.19, J6.1, P7.2, SW1.1 (A), U2.39 (VSYS)
/3V3_EN: J4.17, U2.37 (3V3_EN)
/ADC_VREF: J4.15, U2.35 (ADC_VREF)
/AGND: J4.13, U2.33 (AGND)
/GPIO0: J3.1, U2.1 (GPIO0)
/GPIO1: J3.2, U2.2 (GPIO1)
/GPIO2: J1.1, J3.4, U2.4 (GPIO2)
/GPIO3: J1.2, J3.5, U2.5 (GPIO3)
/GPIO4: J1.3, J3.6, U2.6 (GPIO4)
/GPIO5: J1.4, J3.7, U2.7 (GPIO5)
/GPIO6: J3.9, LS1.1, U2.9 (GPIO6)
/GPIO7: J3.10, R5.1, U2.10 (GPIO7)
/GPIO8: J3.11, SW2.1, U2.11 (GPIO8)
/GPIO9: J3.12, P7.1, U2.12 (GPIO9)
/GPIO10: J3.14, J5.1, U2.14 (GPIO10)
/GPIO11: J3.15, J5.2, U2.15 (GPIO11)
/GPIO12: J3.16, J5.3, U2.16 (GPIO12)
/GPIO13: J3.17, J5.4, U2.17 (GPIO13)
/GPIO14: J3.19, U2.19 (GPIO14)
/GPIO15: J3.20, U2.20 (GPIO15)
/GPIO16: J4.1, U2.21 (GPIO16)
/GPIO17: J4.2, R2.1, U2.22 (GPIO17)
/GPIO18: J4.4, U2.24 (GPIO18)
/GPIO19: J4.5, U2.25 (GPIO19)
/GPIO20: J4.6, U2.26 (GPIO20)
/GPIO21: J4.7, U2.27 (GPIO21)
/GPIO22: J4.9, R4.1, U2.29 (GPIO22)
/GPIO26: J4.11, R3.1, U2.31 (GPIO26_ADC0)
/GPIO27: J4.12, Q2.3 (C), R6.2, U2.32 (GPIO27_ADC1)
/GPIO28: J4.14, Q1.3 (C), R7.2, U2.34 (GPIO28_ADC2)
/RUN: J4.10, U2.30 (RUN)
/VBUS: J4.20, U2.40 (VBUS)
GND: D2.1 (K), D3.1 (K), D4.1 (K), D5.1 (K), J2.2, J3.3, J3.8, J3.13, J3.18, J4.3, J4.8, J4.18, J6.2, LS1.2, P5.2, P7.3, Q1.1 (E), Q2.1 (E), SW2.2, U2.3 (GND), U2.8 (GND), U2.13 (GND), U2.18 (GND), U2.23 (GND), U2.28 (GND), U2.38 (GND)
unnamed: D2.2 (A), R2.2
unnamed: D3.2 (A), R3.2
unnamed: D4.2 (A), R4.2
unnamed: D5.2 (A), R5.2
unnamed: P5.1, P6.2
unnamed: P6.1, SW1.2 (B)

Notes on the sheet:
IR 1.2Vf 330 ohm 12 mA @ 5V
LEFT SIDE RIGHT SIDE
- +
s + -

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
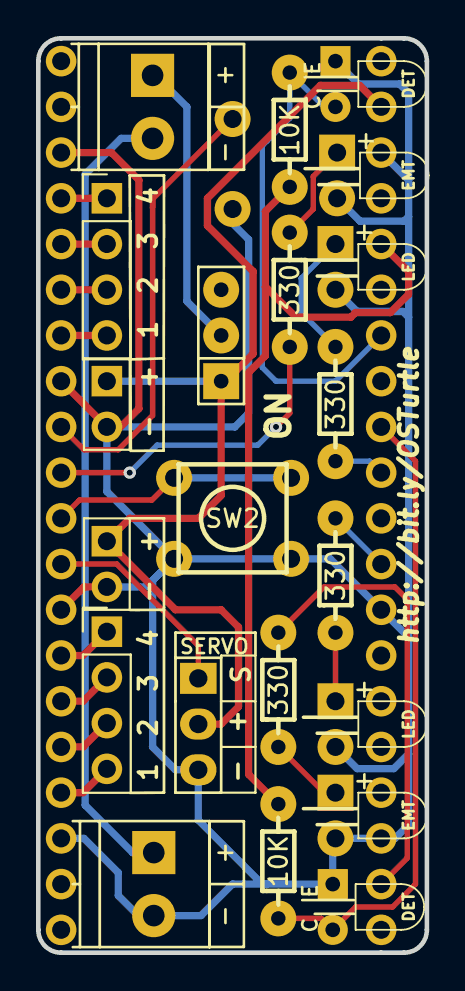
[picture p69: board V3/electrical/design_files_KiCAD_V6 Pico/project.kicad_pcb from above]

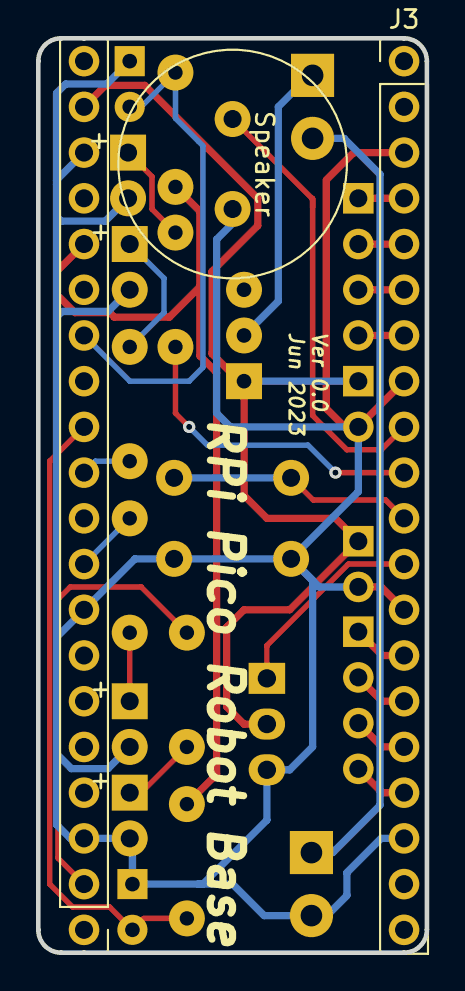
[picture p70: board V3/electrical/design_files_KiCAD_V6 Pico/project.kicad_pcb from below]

Board: 2 copper layers, 21.6 x 50.8 mm, 24 parts (3 on the bottom side), 26 nets.

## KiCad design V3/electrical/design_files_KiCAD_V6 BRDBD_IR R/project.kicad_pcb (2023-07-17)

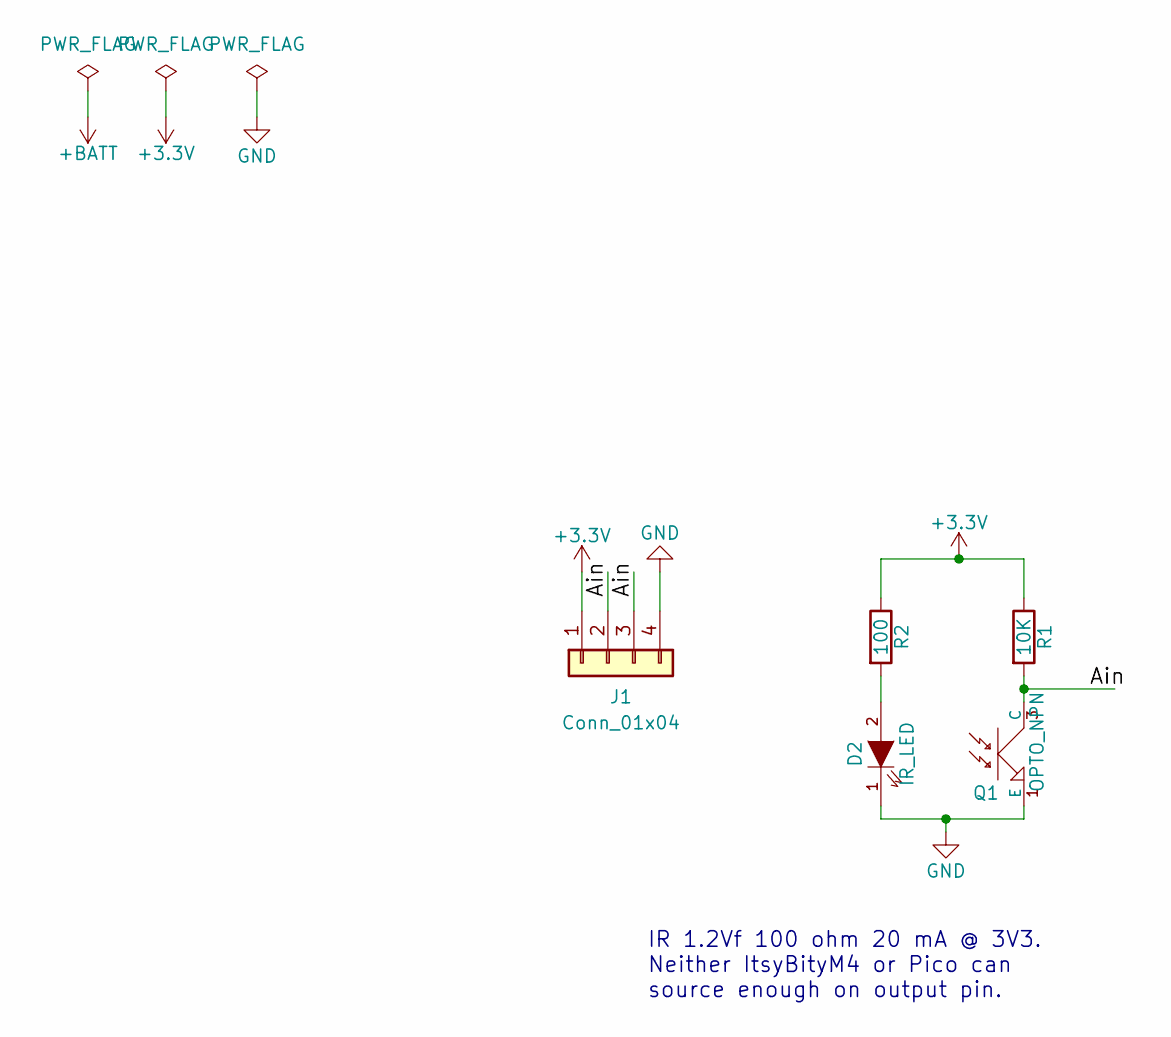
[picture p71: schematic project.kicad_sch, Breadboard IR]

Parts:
D2: IR_LED; LED-3MM_RA
J1: Conn_01x04; PinHeader_1x04_P2.54mm_Vertical
Q1: OPTO_NPN; PHOTOTRANS-RA
R1: 10K; Resistor_Horz
R2: 100; Resistor_Horz

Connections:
+3V3: J1.1, R1.1, R2.1
/Ain: J1.2, J1.3, Q1.3 (C), R1.2
GND: D2.1 (K), J1.4, Q1.1 (E)
unnamed: D2.2 (A), R2.2

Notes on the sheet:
IR 1.2Vf 100 ohm 20 mA @ 3V3. Neither ItsyBityM4 or Pico can source enough on output pin.

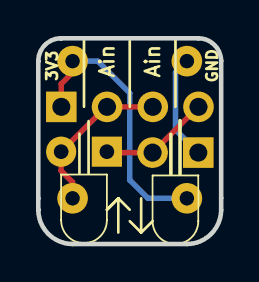
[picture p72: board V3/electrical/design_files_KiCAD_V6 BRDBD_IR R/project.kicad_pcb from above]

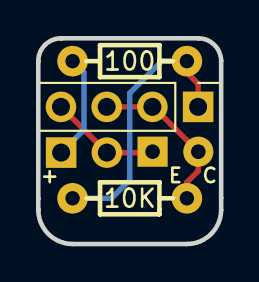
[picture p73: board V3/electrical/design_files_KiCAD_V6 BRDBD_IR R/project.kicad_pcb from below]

Board: 2 copper layers, 10.2 x 11.4 mm, 5 parts (3 on the bottom side), 4 nets.

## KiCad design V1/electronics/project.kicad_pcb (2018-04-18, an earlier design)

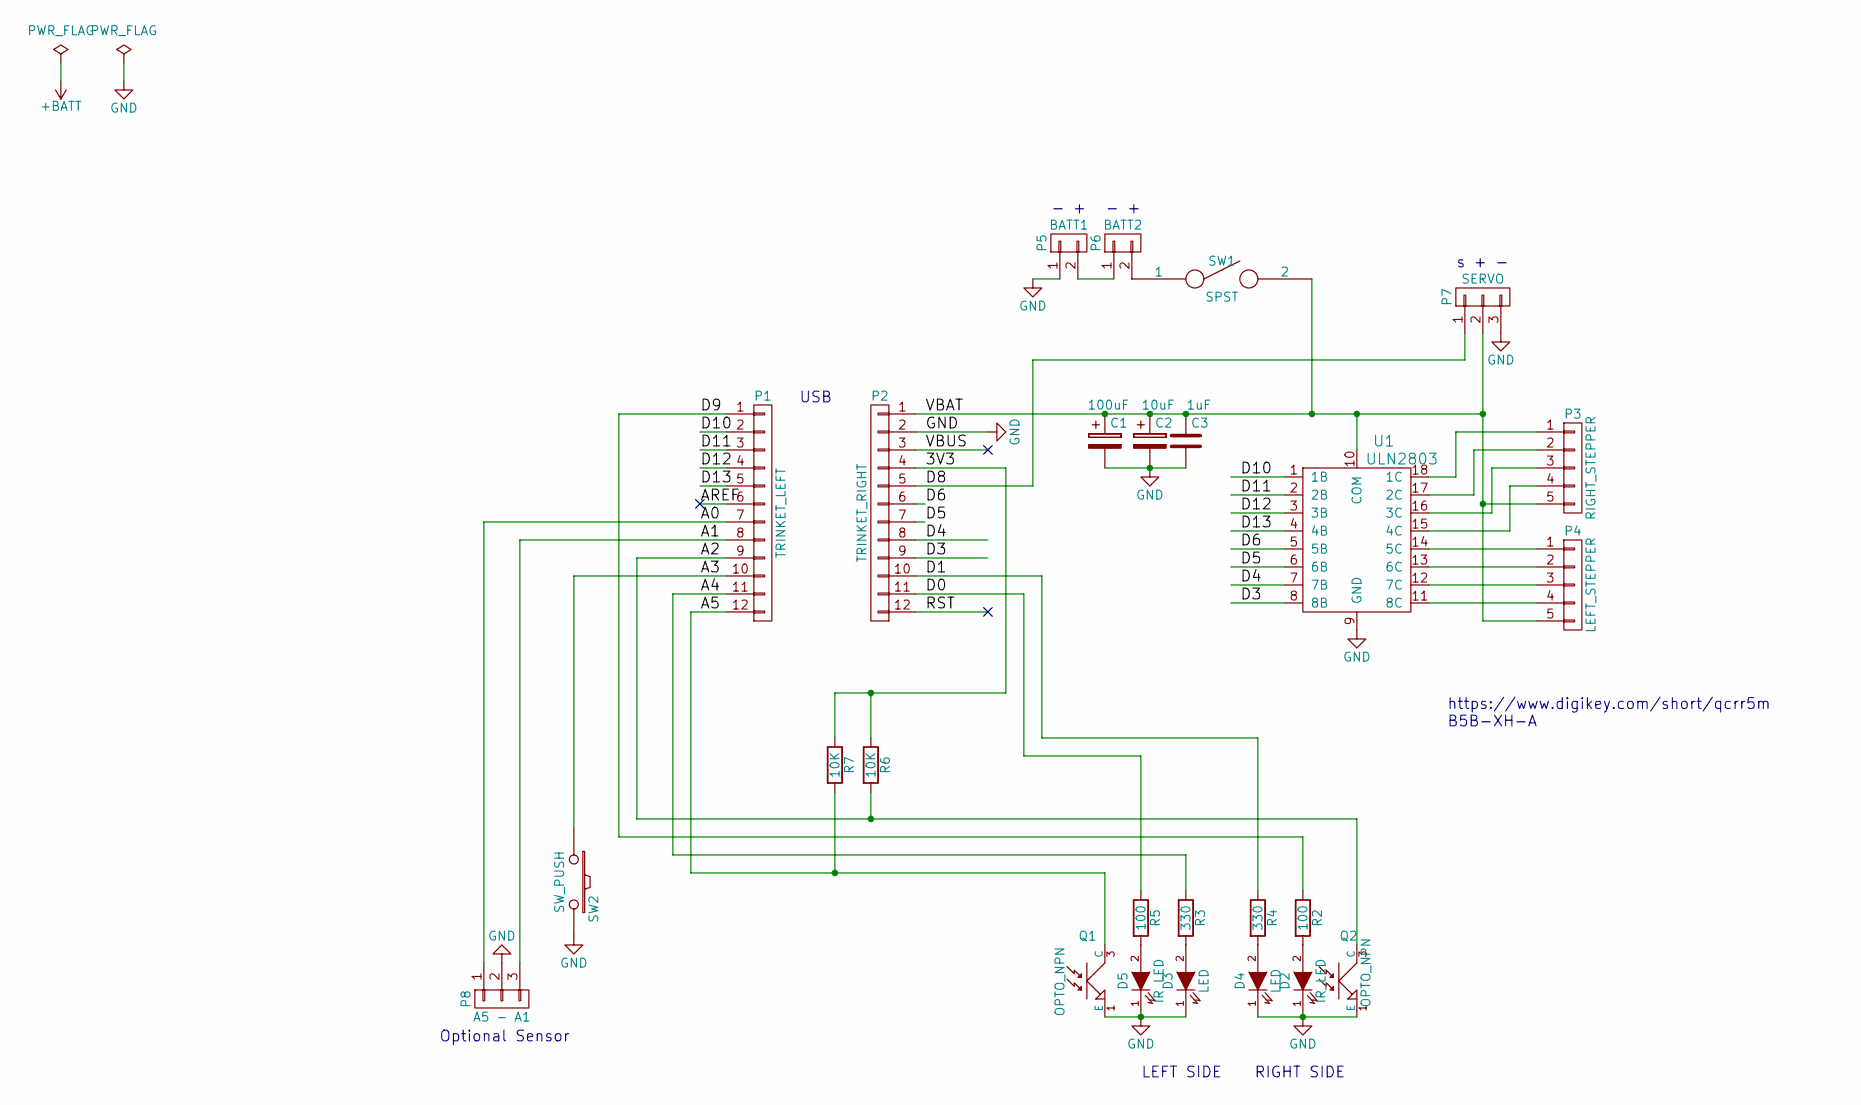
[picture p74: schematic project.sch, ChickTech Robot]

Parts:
C1: 100uF; C_Radial_D7.5_L11.2_P2.5
C2: 10uF; C_Radial_D5_L11_P2.5
C3: 1uF; C_Disc_D3_P2.5
D2: IR_LED; LED-3MM
D3, D4: LED; LED-3MM
D5: IR LED; LED-3MM
P1: TRINKET_LEFT; Pin_Header_Straight_1x12
P2: TRINKET_RIGHT; Pin_Header_Straight_1x12
P3: RIGHT_STEPPER; JST_B5B-XH-A
P4: LEFT_STEPPER; JST_B5B-XH-A
P5: BATT1; TerminalBlock_Pheonix_PT-3.5mm_2pol
P6: BATT2; TerminalBlock_Pheonix_PT-3.5mm_2pol
P7: SERVO; Pin_Header_Straight_1x03
P8: A5 - A1; Pin_Header_Straight_1x03
Q1, Q2: OPTO_NPN; PHOTOTRANS
R2, R5: 100; Resistor_Horz
R3, R4: 330; Resistor_Horz
R6, R7: 10K; Resistor_Horz
SW1: SPST; SW_Micro_SPST
SW2: SW_PUSH; SW_PUSH_SMALL
U1: ULN2803; DIP-18_W7.62mm

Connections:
/3V3: P2.4, R6.1, R7.1
/A0: P1.7, P8.1
/A1: P1.8, P8.3
/A2: P1.9, Q2.3 (C), R6.2
/A3: P1.10, SW2.1
/A4: P1.11, R3.1
/A5: P1.12, Q1.3 (C), R7.2
/AREF: P1.6
/D0: P2.11, R5.1
/D1: P2.10, R4.1
/D3: P2.9, U1.8 (8B)
/D4: P2.8, U1.7 (7B)
/D5: P2.7, U1.6 (6B)
/D6: P2.6, U1.5 (5B)
/D8: P2.5, P7.1
/D9: P1.1, R2.1
/D10: P1.2, U1.1 (1B)
/D11: P1.3, U1.2 (2B)
/D12: P1.4, U1.3 (3B)
/D13: P1.5, U1.4 (4B)
/RST: P2.12
/VBAT: C1.1, C2.1, C3.1, P2.1, P3.5, P4.5, P7.2, SW1.2, U1.10 (COM)
/VBUS: P2.3
GND: C1.2, C2.2, C3.2, D2.1 (K), D3.1 (K), D4.1 (K), D5.1 (K), P2.2, P5.1, P7.3, P8.2, Q1.1 (E), Q2.1 (E), SW2.2, U1.9 (GND)
unnamed: D2.2 (A), R2.2
unnamed: D3.2 (A), R3.2
unnamed: D4.2 (A), R4.2
unnamed: D5.2 (A), R5.2
unnamed: P3.1, U1.18 (1C)
unnamed: P3.2, U1.17 (2C)
unnamed: P3.3, U1.16 (3C)
unnamed: P3.4, U1.15 (4C)
unnamed: P4.1, U1.14 (5C)
unnamed: P4.2, U1.13 (6C)
unnamed: P4.3, U1.12 (7C)
unnamed: P4.4, U1.11 (8C)
unnamed: P5.2, P6.1
unnamed: P6.2, SW1.1

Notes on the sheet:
https://www.digikey.com/short/qcrr5m B5B-XH-A
USB
- +
s + -
Optional Sensor
LEFT SIDE RIGHT SIDE

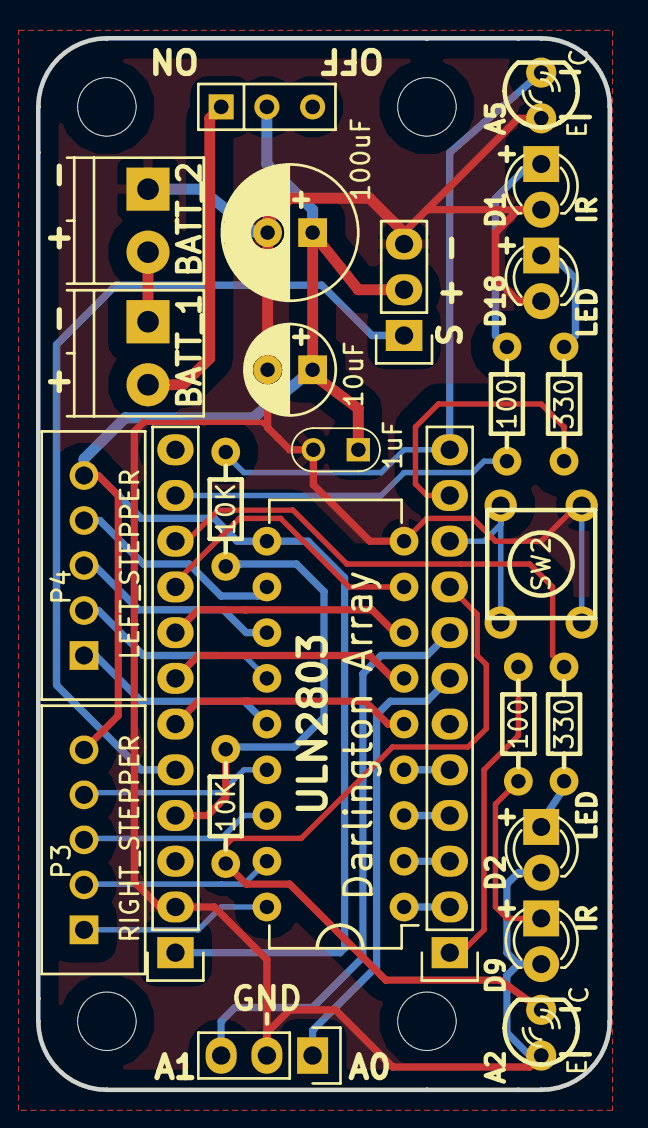
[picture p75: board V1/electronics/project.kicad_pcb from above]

Board: 2 copper layers, 31.8 x 58.4 mm, 32 parts (0 on the bottom side), 35 nets.

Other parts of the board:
P9, P9#2, P9#3, P9#4: CONN_01X01; Lego_Pad
VAL: MadeInOregonRev25
VAL#2: MB225rev

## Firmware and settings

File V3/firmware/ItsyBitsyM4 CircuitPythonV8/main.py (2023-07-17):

'''
Turtle Robot (V3.0) https://github.com/aspro648/OSTR/
@TheMakersBox
#TurtleRobot
648.ken@gmail.com

You have an Adafruit ItsyBitsy M4:
    https://learn.adafruit.com/introducing-adafruit-itsybitsy-m4
Running CiruitPython version 8.2.0
    https://circuitpython.org/board/itsybitsy_m4_express/
With libraries from adafruit-circuitpython-bundle-8.x-mpy-20230709:
    https://github.com/adafruit/Adafruit_CircuitPython_Bundle/releases
Download Mu Editor at https://codewith.mu/en/download

Workshop Links:
  Handouts: https://github.com/aspro648/OSTR/raw/master/V2/docs/Robotics_Handouts.pdf
  Mechanical Assembly: https://github.com/aspro648/OSTR/raw/master/V2/docs/Mechanical_Assembly.pdf


Activites:
  https://www.tinkercad.com/joinclass/6I6RPXA9QDII
  https://groklearning.com/hoc/activity/snowflake/

Turtle Name:  Turtle
Turtle Owner: Your Name
Serial Number: 015
'''

#from turtle import *
from tone import tone         # tone(frequency, duration)
from RGBled import RGBled     # RGBled((red, blue, green))
myColor = (0, 0, 255)       #https://www.rapidtables.com/web/color/RGB_Color.html
RGBled(myColor, brightness=0.15)

print("Hello!  Edit 'code.py' to change the robots behavor.\n")

# Uncomment just code file below that you would like to execute and save this file.
# Click on [Serial] button to see code output.
# Open the individual ".py" file to see what it does or modify it.

import Example_01_blink
# --- The following scripts are Turtle Robot specific ---
#import eye_check
#import example
#import music_example
#import turtle_obstacles

# --- The following will run on the Robot or on a laptop ---
#import turtle_wheel_calibration
#import turtle_snowflake_example1
#import turtle_snowflake_example2
#import turtle_mySnowflake
#import turtle_font_example
#import turtle_cursive_example
#import turtle_goto_example

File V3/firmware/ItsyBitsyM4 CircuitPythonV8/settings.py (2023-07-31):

# robot specific parameters
wheel_dia = 57     # mm (increase = decrease distance)
wheel_base = 106.8  # mm (increase = spiral clockwise)

# stepper parameters
steps_rev = 512    # 512 for 64x gearbox, 128 for 16x gearbox
delay_time = 2     # time between steps in ms (too quick will freeze motors)
invert_direction = False  # change if turtle running backward

# servo parameters
PEN_DOWN = 75     # angle of servo when pen is down
PEN_UP = 160      # angle of servo when pen is up
min_pulse = 750
max_pulse = 2500

DEBUG = True      # Print statements to console

import board

if False: # pins for IstyBitsy M4 Breadboard Robot
    servoPin = board.D7
    speakerPin = board.D5
    buttonPin = board.MISO

    leftLEDPin = board.A2
    rightLEDPin = board.A3
    emitterPin = board.A1

    rightDetectorPin = board.A4
    leftDetectorPin = board.A5

    L_In1_Pin = board.D13  # has onboard LED on it
    L_In2_Pin = board.D12
    L_In3_Pin = board.D11
    L_In4_Pin = board.D10

    R_In1_Pin = board.SCL
    R_In2_Pin = board.SDA
    R_In3_Pin = board.D1
    R_In4_Pin = board.D0

else: # pins for Turtle Robot Base Kit
    servoPin = board.A1
    speakerPin = board.A0
    buttonPin = board.D12

    leftLEDPin = board.D7
    rightLEDPin = board.D11
    emitterPin = board.D5

    rightDetectorPin = board.A2
    leftDetectorPin = board.A3

    L_In1_Pin = board.D13  # has onboard LED on it
    L_In2_Pin = board.D10
    L_In3_Pin = board.A4
    L_In4_Pin = board.A5

    R_In1_Pin = board.SCK
    R_In2_Pin = board.MOSI
    R_In3_Pin = board.MISO
    R_In4_Pin = board.D9

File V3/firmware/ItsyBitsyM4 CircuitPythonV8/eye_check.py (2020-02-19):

import board
import digitalio
from time import sleep
from analogio import AnalogIn
from turtle import *

# The LED will indicate when an object is close enough to reflect IR back to the detector.
# With board attached to computer, lanuch plotter in Mu to see graphical response rates.

print('\nRunning "turtle_eye_check.py"')
print('Click on the [Plotter] button to see a graph of the output.')
print('Turtle robot shield must be attached.')
print('What happens when you hold your hand in front of the clear LED?')

UP = True     # some alias to help track pen position
DOWN = False
penState = UP

# Turn IR LEDs on.  You might be able to see them in a camera.
emitter.value = True

for x in range(3):  # blink front LEDs 3 times
    rightLED.value = True
    leftLED.value = True
    sleep(0.25)
    rightLED.value = False
    leftLED.value = False
    sleep(0.25)

while True:
    rightVal = rightDetector.value / 65535  # The analog value is 12-bits, thus 0 - 65535
    leftVal = leftDetector.value / 65535    # We convert it to a ratio to make it easier to read.
    if rightVal > 0.5:
        rightLED.value = False  # Turn LED off
    else:
        rightLED.value = True   # Or turn in on.
    if leftVal > 0.5:
        leftLED.value = False
    else:
        leftLED.value = True

    if (isButtonPushed()):
        while(isButtonPushed()):
            time.sleep(0.1)
        penState = not(penState)
        if penState:
            penup()
        else:
            pendown()

    print('(%.2f, %.2f, %d)' % (leftVal, rightVal, isButtonPushed()))  # Formats output to two decimal places
    sleep(0.1)  # Don't go too fast if we're trying to read the output!

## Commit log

2018-04-18 Update PCB link and BOM
    [project.kicad_pcb, project.sch]
2018-04-22 Updated BOM, labels
2018-04-27 Updated nameplate & chassis
    [Chassis_V02.scad, Chassis_V02.stl, Name_Plate_V01.stl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]
2018-05-25 Updated firmware and mechanicals
    [Chassis_Tinsy_V0.scad, Chassis_Tinsy_V0.stl, Chassis_V03.stl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]
2018-10-23 Updted BOM
    [Workshop BOM.ods]
2018-10-26 Updating Read.me. Not a big fan of markdown.
2019-11-18 Firmware and BOM updates
2019-11-27 Merge branch 'master' of https://github.com/aspro648/OSTR
    # Conflicts:
    # V2/firmware/CircuitPython M4/turtle_wheel_calibration.py
2020-02-17 V2.2 pannel for fab
    [base-B.Cu.gbl, base-B.Mask.gbs, base-B.SilkS.gbo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]
2020-10-23 Updating BOM
2023-07-17 V3 Updates
    [1-2834016-4.step, 1984617.stp, 1988969.stp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]
